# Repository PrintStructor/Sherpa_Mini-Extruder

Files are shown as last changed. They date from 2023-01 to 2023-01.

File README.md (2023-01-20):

# Sherpa Mini - Release 1

## FAQ
For Material Requirements, Print Settings and How to Interpret the file naming structure, please see: "Print_Settings_and_File_Key.txt"

The BOM and Sourcing Guide for this product can be found here: https://docs.google.com/spreadsheets/d/1O3eyVuQ6M4F03MJSDs4Z71_XyNjXL5HFTZr1jsaAtRc/edit?usp=sharing

## Product Info
This is the Sherpa Mini Extruder, a ground up design developed by Anlin and the team at Annex Engineering. It's a dual geared hobbed filament extruder designed for use with any printer. It features a 50:10 or a 50:8 gear driven design to provide torque while being able to be near silent. You must perform your own tuning to get the best results.

A Pinion Equipped Pancake Stepper is required for this Release.

Our discord server can be found here: 

Join me on Discord (https://discord.gg/MzTR3zE)

Image of Sherpa Extruder

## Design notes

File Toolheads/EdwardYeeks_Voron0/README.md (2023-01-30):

# V0 Toolhead for Sherpa Mini - Beta 1

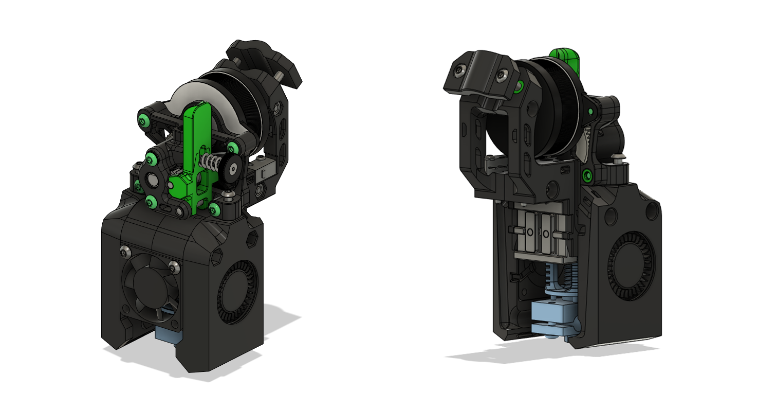
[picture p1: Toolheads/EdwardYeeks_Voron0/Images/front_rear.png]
V0 Toolhead Front


This is Beta 1 release of the V0 toolhead to mount the Sherpa Mini Extruder as a direct drive extruder. Compared to the Alpha 2, the changes in this release are:

- Sherpa Mini is lowered 2mm closer to the hotend, reducing the distance between the extruder and hotend as well as the total height of the assembly slightly.
- New umbilical strain relief with options to use a printed clamp that screws together or zipties. Compared to the previous versions, this provides a lot more support as well as much more room to work with. The 30° angle forwards provides more bending radius for the umbilical cable when the toolhead is at Y max/rear.

<p align="center">
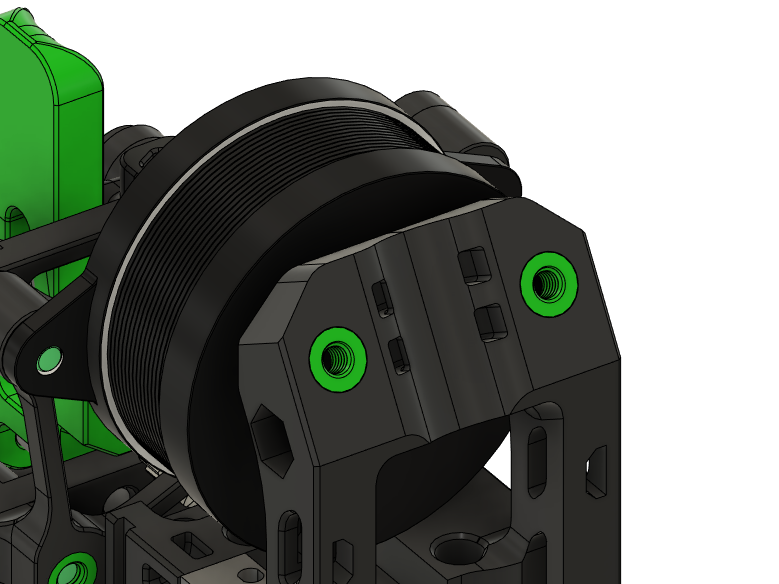
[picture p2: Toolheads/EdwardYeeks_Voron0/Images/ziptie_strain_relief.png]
  
</p>

- More ziptie points as well as small tweaks to make them less prone to breaking.

Stock fan ducts are available and the CAD files for the toolhead has been included if you wish to tinker with it (feel free to add your own features and logos). For the length of the bowden tube between the sherpa mini and the hotend, use the following lengths as a starting point:

- V6 Threaded: **39mm**
- Mosquito: **23mm**
- Dragon: **24mm**

You will need a [Sherpa Mini](https://github.com/Annex-Engineering/Sherpa_Mini-Extruder) and its parts can be found in our [sourcing guide](https://docs.google.com/spreadsheets/d/1O3eyVuQ6M4F03MJSDs4Z71_XyNjXL5HFTZr1jsaAtRc/htmlview#). It reuses all the same fasteners and parts from the original V0 toolhead with exception of the following extra parts:

- 4x Heatset inserts (3x5x4mm) (2x only needed if using ziptie to provide strain relief to umbilical cable.)
- 1x M3x25mm bolt and 1x M3 nut
- 2 M3x16mm bolts (optional, used only with cable clamp.)

*Note: There is no direct comparison between the stock fan duct and the focussed fan duct yet. However, the focussed fan duct has been tested and works well in my setup.*

Assembled Toolhead Pictures
<sub>You may want to assembled your nema 14 motor such that the wires exit from beneath the sherpa mini, creating a more neater look. </sub>

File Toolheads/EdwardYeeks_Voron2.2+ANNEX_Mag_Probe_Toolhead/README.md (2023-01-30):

# V2.2 Toolhead for Sherpa Mini - Release 2

This is a toolhead and X carriage for the Sherpa Mini Extruder based off the original V2.2 design. Compared to the original toolhead, the blower fans have been moved forward by 4mm to provide clearance for V1.8/V2.4 gantries while still clearing the front panel at Y-min. It is a dual rail variant. Single rail variants will be added in the future.

It is a direct drop in for V2.2, V2.4 and Denali gantries. For V1.8, a loss of ~2-4mm in the x-axis total travel is expected.

It supports the Dragon Hotend and Mosquito Hotend (for E3D V6 mounts, refer to papejelly's mount [here](https://github.com/Annex-Engineering/Sherpa_Mini-Extruder/tree/master/Toolheads/PapeJelly_VORON2.2_V6)). For probes, only the Omron TL-Q5MC2 probe and the Magnetic Microswitch probe from Annex are supported. There is also X carriage options that have microswitch mounting points making them compatible with Denali/V1.8 gantry; you need only choose and print the right X carriage for these printers.

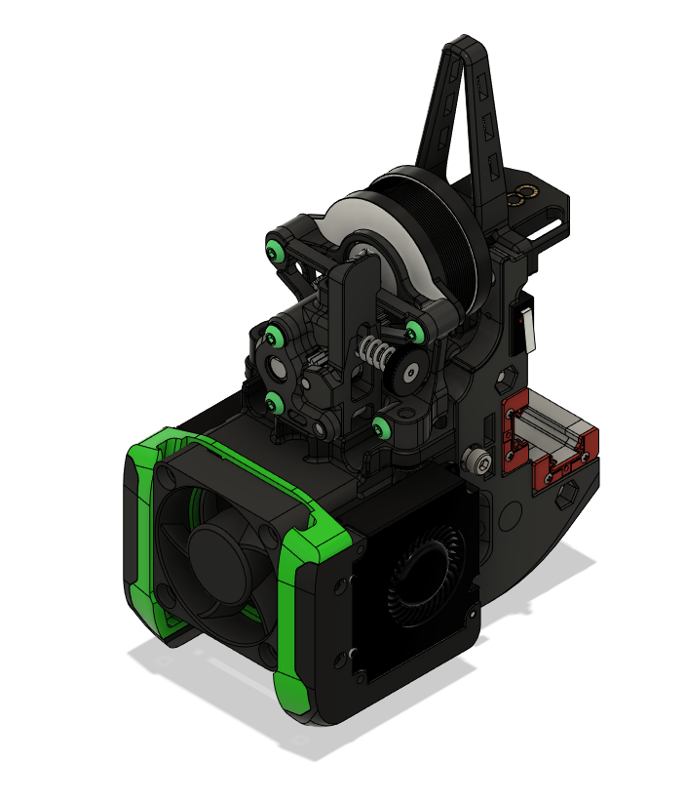
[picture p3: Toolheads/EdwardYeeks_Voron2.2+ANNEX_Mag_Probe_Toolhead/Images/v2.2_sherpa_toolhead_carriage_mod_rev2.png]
Image of V2.2 X Carriage


## Parts Required

Refer to our [sourcing guide](https://docs.google.com/spreadsheets/u/1/d/1O3eyVuQ6M4F03MJSDs4Z71_XyNjXL5HFTZr1jsaAtRc/htmlview#) for recommended vendors. CAD is also provided to allow you to view the assembly and parts.

**Required**
- 2x M3X16mm SHCS
- 4x M3X12mm SCHS
- 2x M3X16mm SHCS
- 3x M3x30mm SHCS
- 6x M3X8mm SHCS
- 4X M3X6mm BHCS
- 10x M2X8mm self tapping screws
- 2x M3 OpenBuilds M3 Tee Nuts (for belt clamps, you can reuse the printed belt clamps from Voron Afterburner/older 2.2 toolheads)
- 6x M3 nuts
- 10X Heatset Inserts (3x5x4mm)
- 1x 4010 axial fan (hotend cooling)
- 2x 4010 blower fan (parts cooling)
- Wire connectors of your choice

**Optional depending on toolhead & mounts**
- 1x M3X20mm SCHS (for Omron X-Carriage only)
- 1x extra M3x30mm SHCS (for Omron X-Carriage)
- 2x extra M2X8mm self tapping screws (for Denali/V1.8 carriage only, to mount the microswitch)
- 1x Omron TL-Q5MC2 probe (for omron carriage option)
- 4x 3x6mm magnets (for magnetic microswitch carriage only)

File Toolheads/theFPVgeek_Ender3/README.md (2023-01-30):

Sherpa Mini Ender3 Mount
- can be used with stock hotend & fan setup
- built in wire management

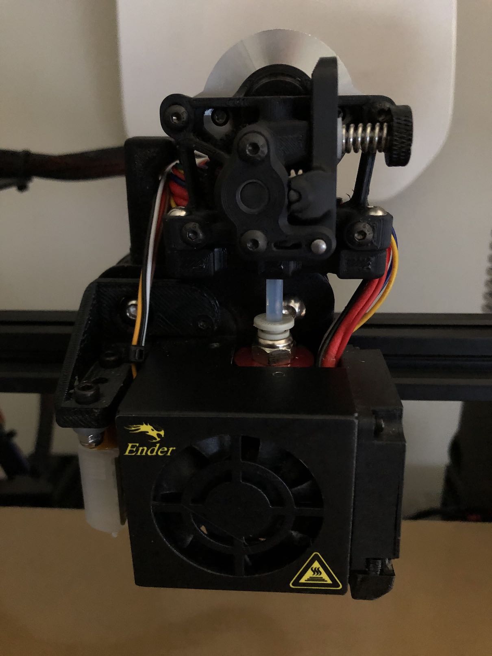
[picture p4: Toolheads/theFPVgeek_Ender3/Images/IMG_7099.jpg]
Image of Ender Mount


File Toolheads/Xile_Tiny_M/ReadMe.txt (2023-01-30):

This is a toolhead carriage combo for Tiny-M, utilizing the Sherpa Mini extruder as a direct drive option. I have opened up the parts cooling fan spacing to allow for a easier time installing
the cooling fans. Also added zip tie slots to allow for some cable managment from the hotend.

Special thank you to discord user wenndemann for his work on the Mosquito toolhead!

Happy printing!

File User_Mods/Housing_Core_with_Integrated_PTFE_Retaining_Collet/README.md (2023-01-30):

# Housing Core with Integrated PTFE Retaining Collet

This is a modification of the housing core *revision 4*, namely *housing_core_x1_rev4.STL* mesh, that adds an integrated PTFE retaining collet for a more simple PTFE tube handling.

The modification is designed around a collet like the E3D ones, see picture below.

**It has not been tested yet**.

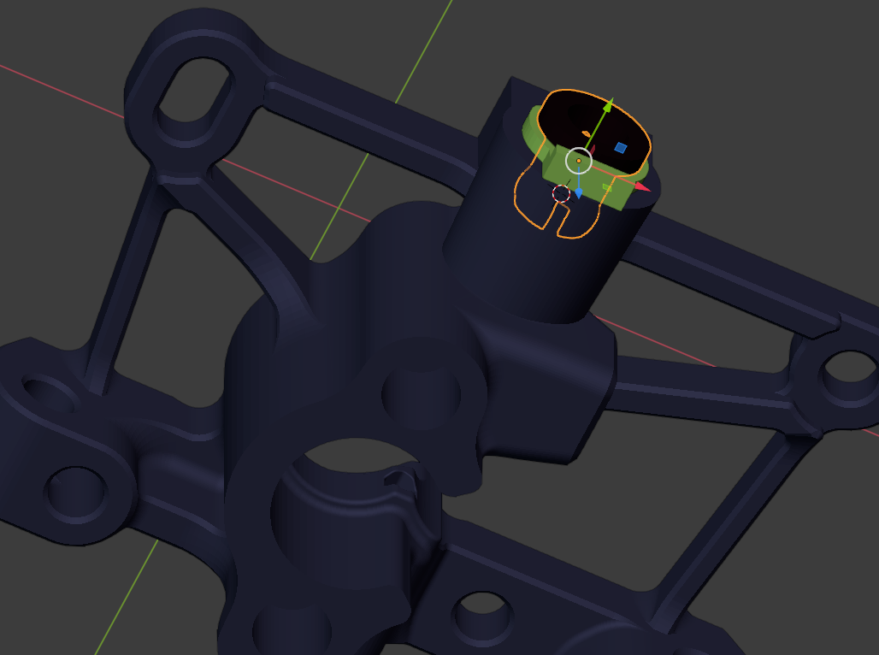
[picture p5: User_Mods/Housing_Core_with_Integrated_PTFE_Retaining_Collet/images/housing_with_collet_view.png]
Image of Housing with PTFE Collet


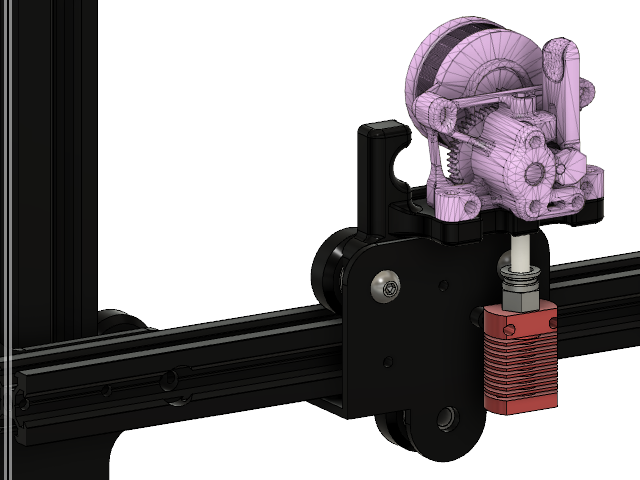
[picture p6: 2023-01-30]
Toolheads/theFPVgeek_Ender3/Images/Sherpa-Mini-StockHead v10.png

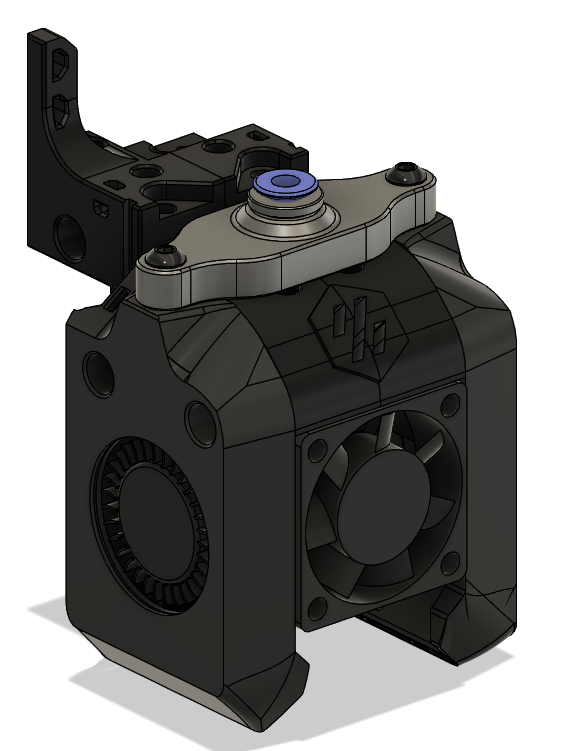
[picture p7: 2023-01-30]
Toolheads/Hartk1213_Bowden_Adapter_Voron0/Images/unknown-23.png

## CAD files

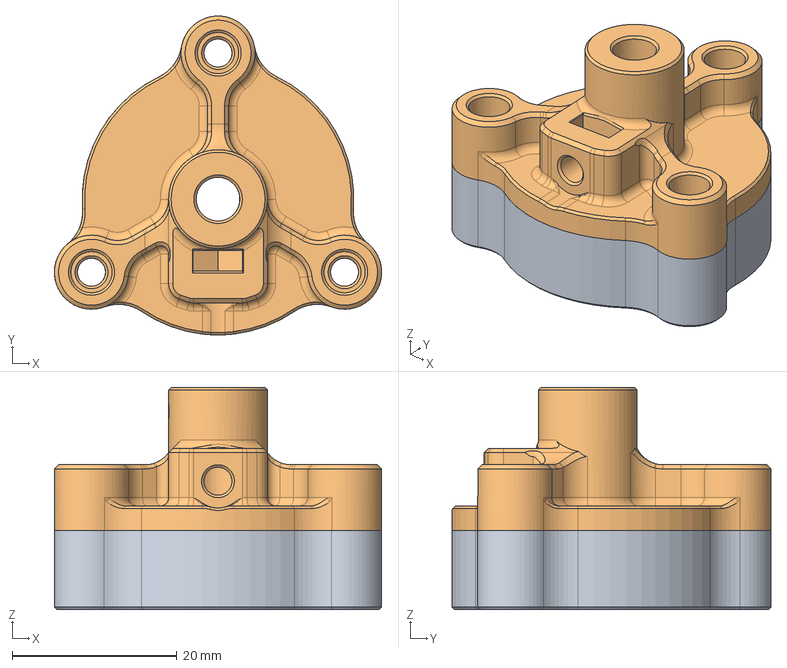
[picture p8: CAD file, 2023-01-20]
Assembly_Tools/Shaft_Grinding_Tool/shaft_block v4.step
39.8 x 38.8 x 27.0 mm
bottom
top

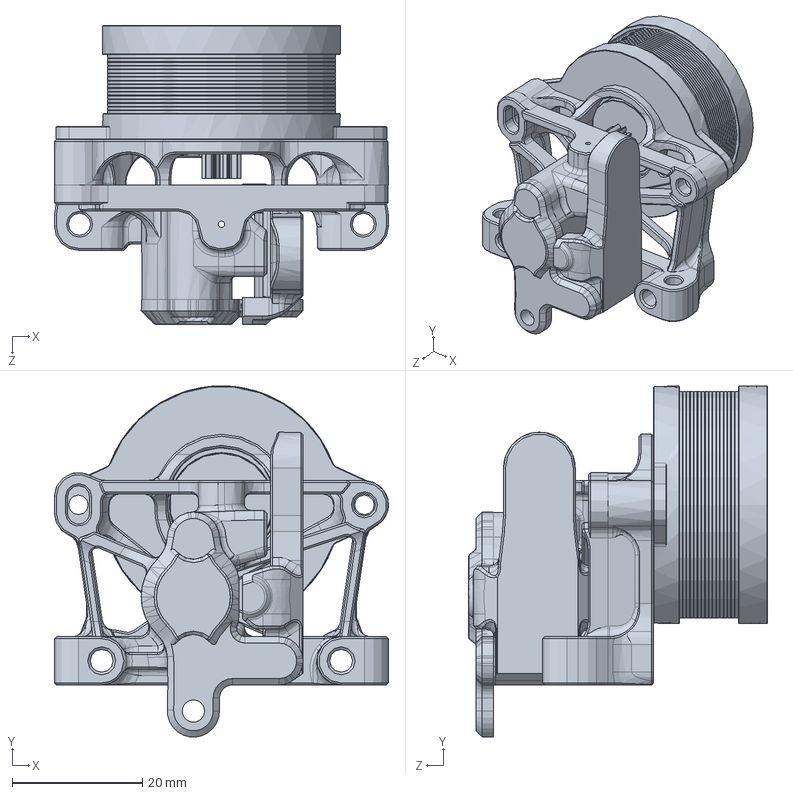
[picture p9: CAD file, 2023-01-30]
Mockup_CAD/sherpa_mini_b3_mockup.SLDPRT
51.2 x 53.8 x 45.9 mm

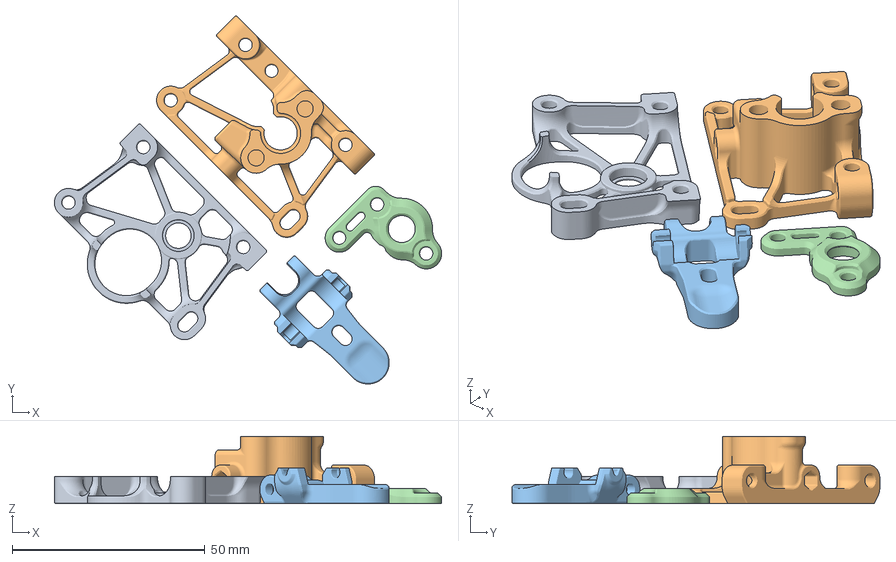
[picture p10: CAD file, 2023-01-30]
STLs/FDM_STLs/Sherpa Printparts.3mf
100.6 x 95.6 x 17.5 mm
housing_rear_bt_x1_rev1.STL
housing_core_bt_x1_rev1.STL
[a]_idler_arm_long_x1_rev5.STL
[a]_housing_front_x1_rev5.STL

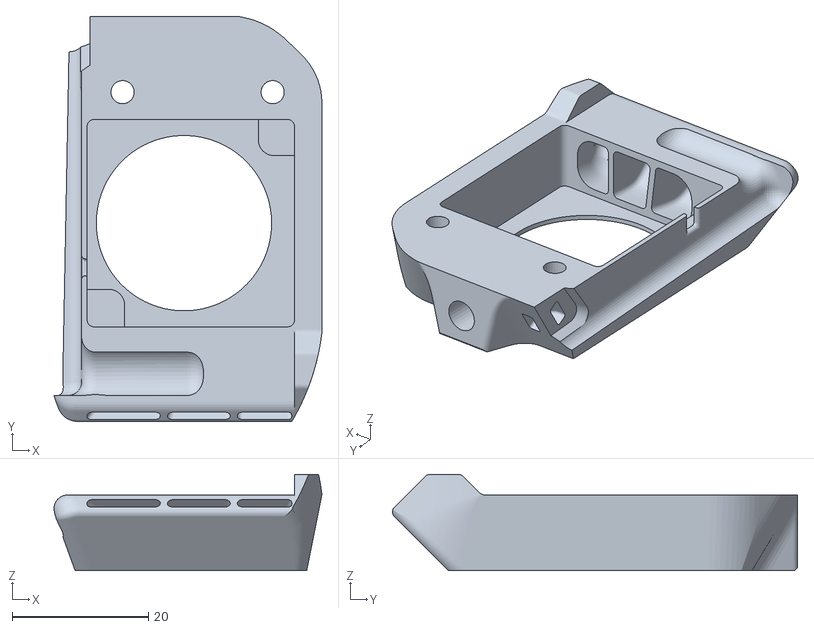
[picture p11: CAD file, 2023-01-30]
Toolheads/EdwardYeeks_Voron0/STLs/cooling_fan_duct_stock_right_rev1.stl
39.3 x 59.4 x 14.1

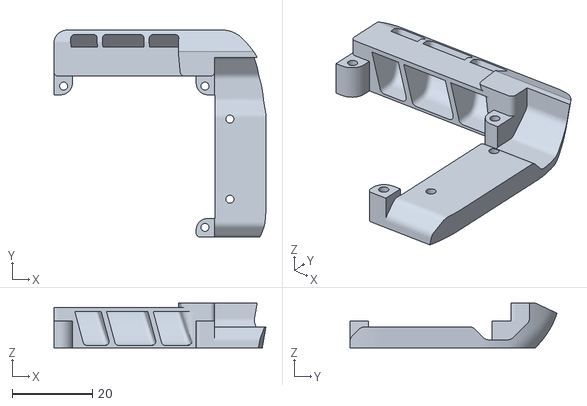
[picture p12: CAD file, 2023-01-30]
Toolheads/EdwardYeeks_Voron2.2+ANNEX_Mag_Probe_Toolhead/STLs/4010_cooling_duct_focussed_left_rev3.stl
52.8 x 51.6 x 11.1

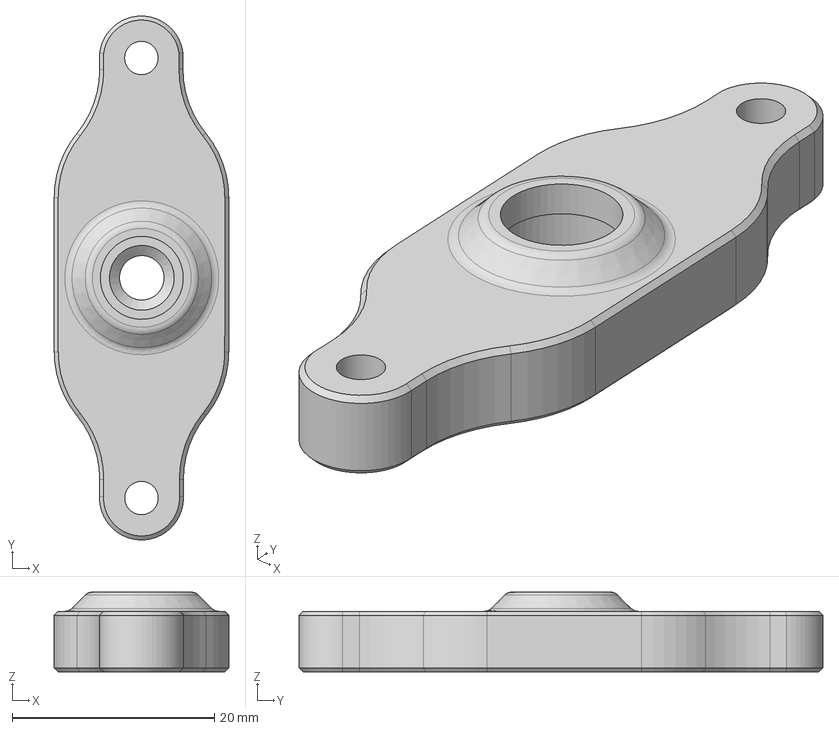
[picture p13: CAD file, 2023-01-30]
Toolheads/Hartk1213_Bowden_Adapter_Voron0/CAD/SherpaBowden.step
17.3 x 51.8 x 7.90 mm

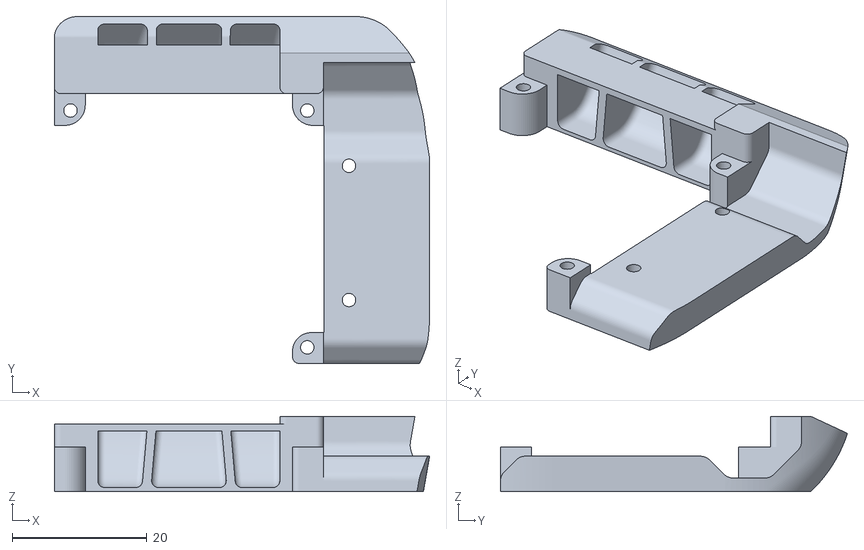
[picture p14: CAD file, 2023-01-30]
Toolheads/PapeJelly_VORON2.2_V6+ANNEX_Mag_Probe_Toolhead/STL's/4010_radial_fanduct_focussed_left.STL
55.8 x 51.6 x 11.1

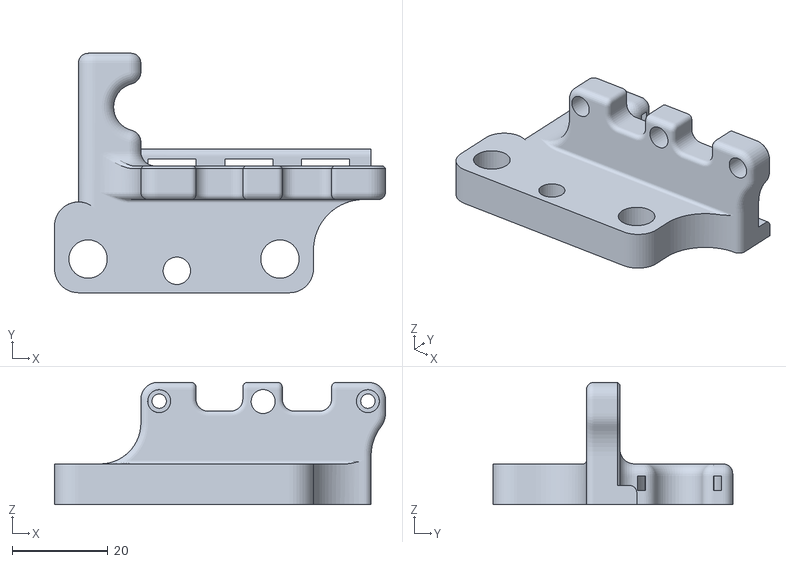
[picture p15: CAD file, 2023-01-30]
Toolheads/theFPVgeek_Ender3/STLs/Ender3-SherpaMini-Mount-v1.stl
69.0 x 49.9 x 25.5

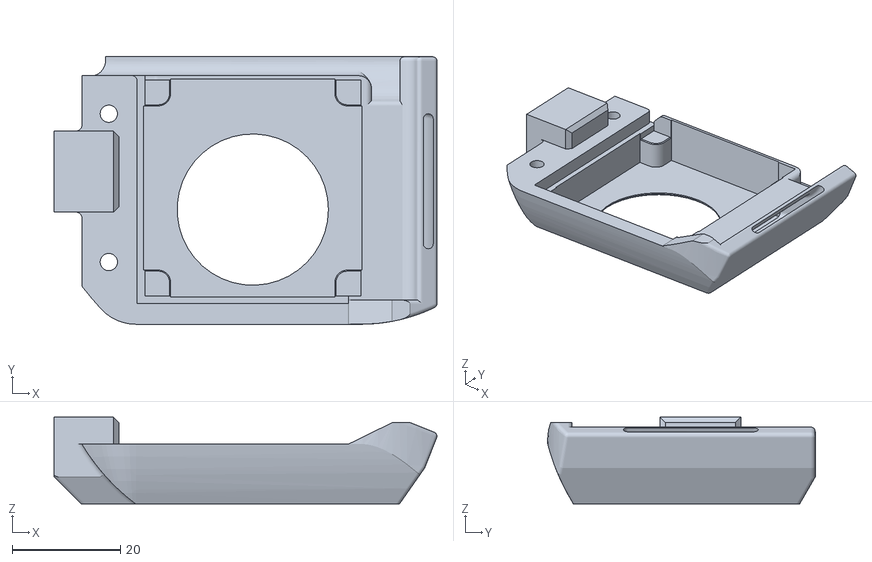
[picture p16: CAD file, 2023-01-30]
Toolheads/Xile_Tiny_M/Dragon Toolhead/STL/fanduct_left.STL
70.9 x 49.5 x 16.1

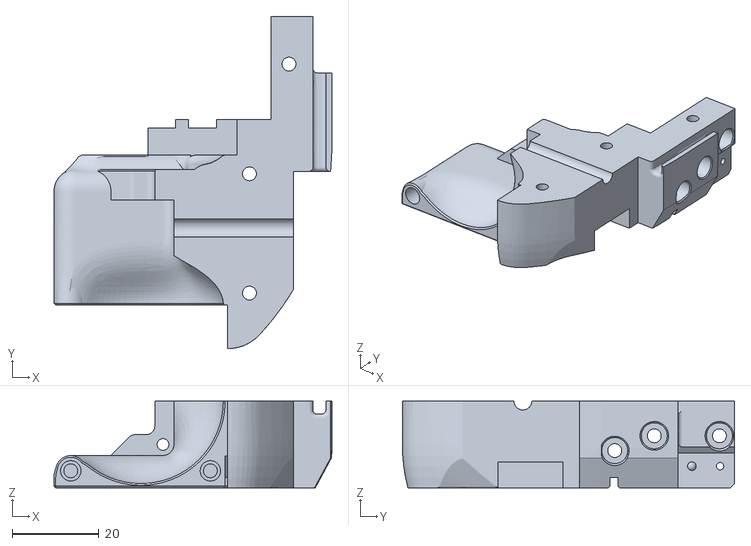
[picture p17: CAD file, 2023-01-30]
Toolheads/Xile_Tiny_M/Mosquito Toolhead/STL/carriage_right.STL
64.0 x 76.5 x 20.0

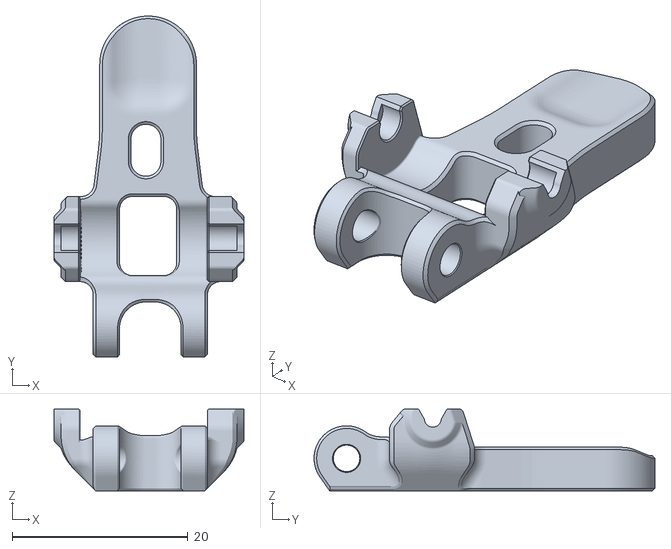
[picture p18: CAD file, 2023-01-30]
User_Mods/4.6mm OD Inserts mod/stls/idler_arm_long.STL
21.6 x 38.8 x 9.30

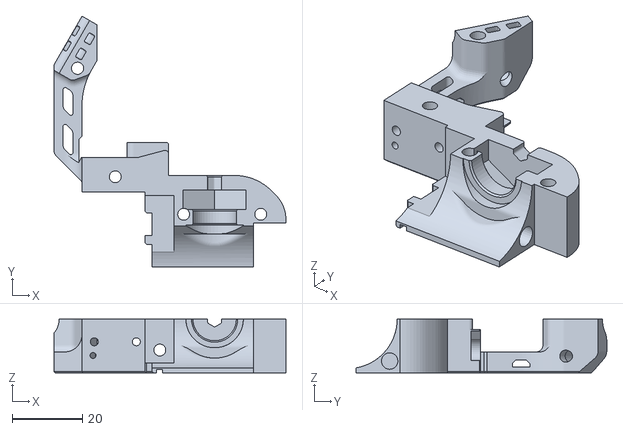
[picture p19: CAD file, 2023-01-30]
Toolheads/EdwardYeeks_Voron0/STLs/v6_toolhead_right_rev1.stl
66.2 x 71.5 x 15.4

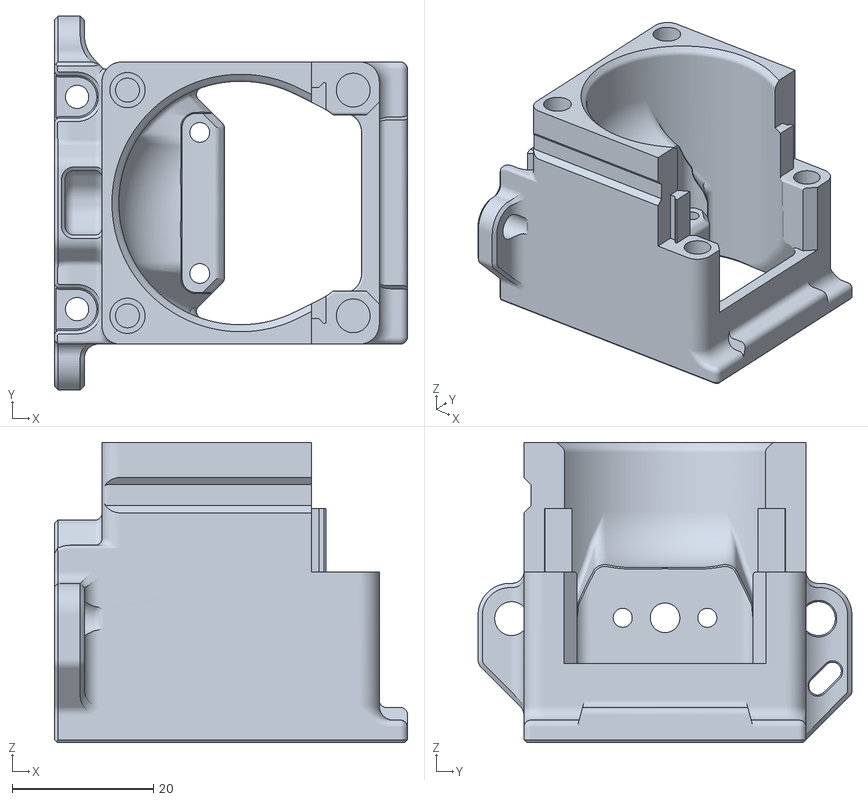
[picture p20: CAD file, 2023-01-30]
Toolheads/EdwardYeeks_Voron2.2+ANNEX_Mag_Probe_Toolhead/STLs/mosquito_sherpa_mini_mount_rev1.STL
50.0 x 53.0 x 42.6

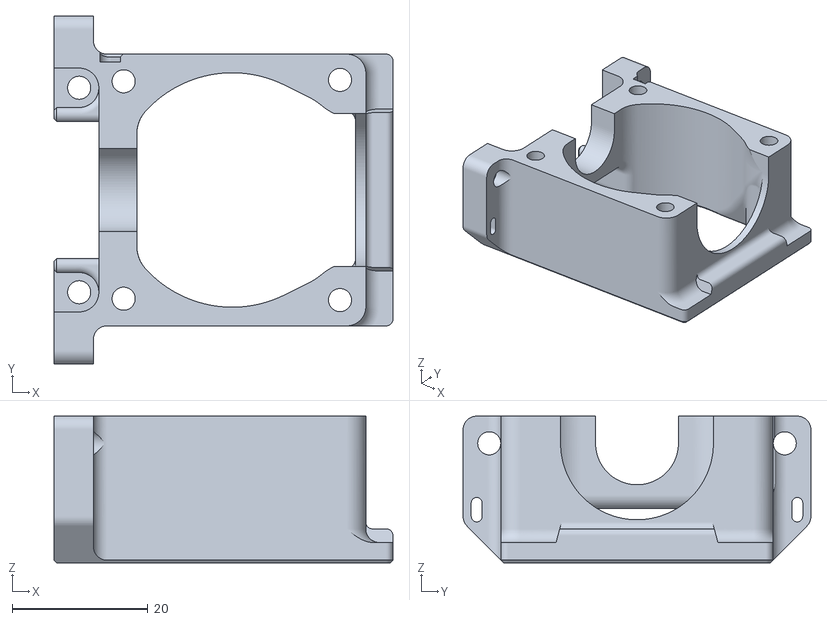
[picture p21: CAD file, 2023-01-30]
Toolheads/PapeJelly_VORON2.2_V6+ANNEX_Mag_Probe_Toolhead/STL's/V6_sherpa_mini_mount_back.STL
49.9 x 51.2 x 21.6

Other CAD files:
Toolheads/Xile_Tiny_M/Dragon Toolhead/STL/carriage_left.STL
Toolheads/Xile_Tiny_M/Mosquito Toolhead/STL/carriage_left.STL
User_Mods/4.6mm OD Inserts mod/stls/housing_front_k.STL
Toolheads/EdwardYeeks_Voron0/STLs/mosquito_toolhead_left_rev1.stl
Toolheads/EdwardYeeks_Voron0/STLs/cooling_fan_duct_focussed_left_rev2.stl
Toolheads/EdwardYeeks_Voron0/STLs/cooling_fan_duct_focussed_right_rev1.stl
Toolheads/EdwardYeeks_Voron0/STLs/cooling_fan_duct_stock_left_rev1.stl
Toolheads/EdwardYeeks_Voron0/STLs/dragon_toolhead_left_rev1.stl
Toolheads/EdwardYeeks_Voron0/STLs/dragon_toolhead_right_rev1.stl
Toolheads/EdwardYeeks_Voron0/STLs/mosquito_toolhead_right_rev1.stl
Toolheads/EdwardYeeks_Voron0/STLs/umbilical_strain_relief_clamp_rev1.stl
Toolheads/EdwardYeeks_Voron0/STLs/v6_toolhead_left_rev1.stl
Toolheads/EdwardYeeks_Voron2.2+ANNEX_Mag_Probe_Toolhead/STLs/4010_cooling_duct_focussed_right_rev3.stl
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

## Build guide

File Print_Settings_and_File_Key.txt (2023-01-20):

Primary Color: nothing at start of file name
Accent Color: [a]_ at start of file name
Quantity Required: _x# near end of file name
File Revision: _Rev# at end of file name

Nozzle Size: 0.5mm 
Recommended FDM Materials: ASA, Polymaker or 3DXTech Recommended
Alternate Approved FDM Materials: PC, 3DXTech Recommended
Layer Height: 0.25mm
Extrusion Width: Forced 0.5mm
Infill Percentage: 40% minimum (at 0.8mm Width)
Infill Type: Grid, Gyroid, Honeycomb, Triangle or Cubic
Wall Count: 3 minimum (at 0.5mm Width)
Solid Top/Bottom Layers: 4 minimum (at 0.5mm Height)

Nozzle Size: 0.4mm 
Recommended FDM Materials: ASA, Polymaker or 3DXTech Recommended
Alternate Approved FDM Materials: PC, 3DXTech Recommended
Layer Height: 0.20mm or 0.25mm
Extrusion Width: Forced 0.4mm
Infill Percentage: 40% minimum (at 0.6mm Width)
Infill Type: Grid, Gyroid, Honeycomb, Triangle or Cubic
Wall Count: 4 minimum (at 0.4mm Width)
Solid Top/Bottom Layers: 4 minimum (at 0.25mm Height)

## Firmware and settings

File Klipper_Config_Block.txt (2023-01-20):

These are good starting settings for the extruder, I have copy pasted my entire block out of my klipper config below:

# Extruder0
[extruder]
rotation_distance: 22.67895 #for 5mm Shaft Driven Bondtech gearsets
#gear_ratio: 50:10 #for standard 10t motor
gear_ratio: 50:8 #for sherpa mini 8t motor
microsteps: 16
full_steps_per_rotation: 200 #1.8deg Motor

max_extrude_only_distance: 1400.0
max_extrude_only_velocity: 75.0
max_extrude_only_accel: 1500

#settings for NEMA14 Stepper
[tmc2209 extruder]
interpolate: True

#Run current is listed in RMS
run_current: 0.30 #min current, equivalent to 0.42A peak (Peak = RMS/0.707)
#run_current: 0.35 #max current, equivalent to 0.49A peak (Peak = RMS/0.707)

#starting point for retraction tuning
#retraction speed: 30mm/s - do not exceed this speed
#retraction distance: 0.4mm

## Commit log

2023-01-20 .
    .
    [Klipper_Config_Block.txt, shaft_block v4.step]
2023-01-30 Combined Versions
    [4010_cooling_duct_focussed_left_rev3.stl, 4010_cooling_duct_focussed_right_rev3.stl, 4010_radial_fanduct_focussed_left.STL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]
